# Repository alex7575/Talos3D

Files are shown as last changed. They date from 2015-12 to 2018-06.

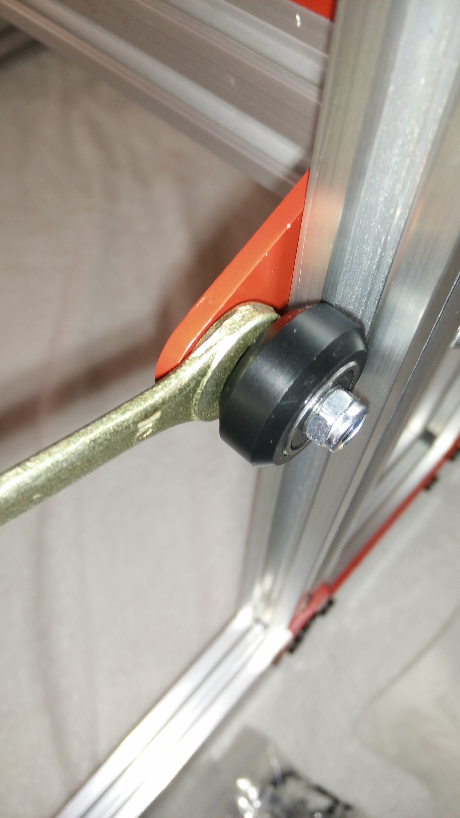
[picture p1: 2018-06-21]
Spartan/Pictures and Video/Assembly Images/IMG_20151225_152253.jpg

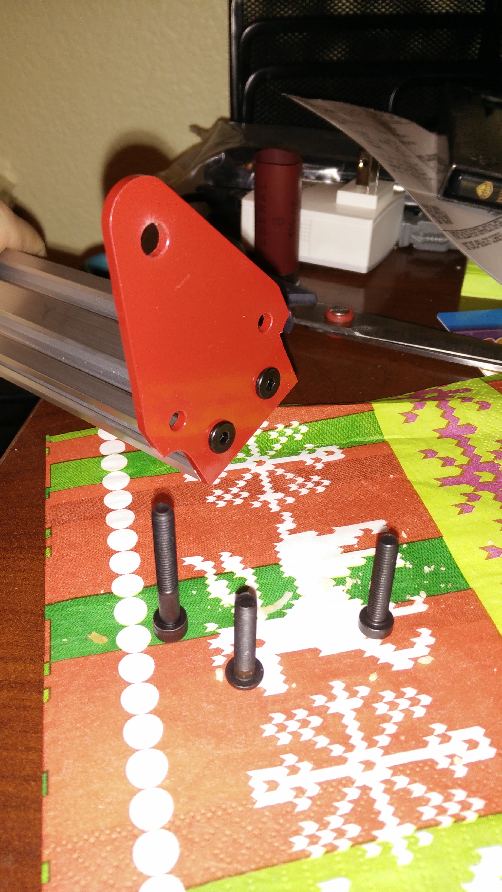
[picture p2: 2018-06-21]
Spartan/Pictures and Video/Assembly Images/IMG_20151224_170027.jpg

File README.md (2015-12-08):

# Talos3D

Please join us at our <a href="https://plus.google.com/u/0/communities/106411395795447750286">G+ group</a>



## Assembly

### Generating a Design
TODO

### Printing

### Tutorial

TODO: Tutorial on how to actually make these.

## License

All sources distributed under the [Creative Commons Attribution-NonCommercial-ShareAlike License Version 3.0](LICENSE-models).

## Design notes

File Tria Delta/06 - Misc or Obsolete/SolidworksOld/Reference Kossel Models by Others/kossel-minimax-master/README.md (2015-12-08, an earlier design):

###Kossel Minimax

Based on Johan's Kossel Mini @ github.com/jcrocholl/kossel/

Completely remodeled in Solidworks for Misumi 2020 and 2040 extrusions and a much bigger print area (300mm diameter print plate, ~470mm cylindrical print height, ~500mm tower print height, 1000mm overall height)

**Basic BOM:**

For belts, thid design uses 2020mm GT2 belts for each axis, 6060mm total, get a bit more to be safe.

* Aluminum Extrusion 2020 (length 420mm qty3 and length 1000mm qty3) (http://us.misumi-ec.com/vona2/detail/110302368740/ Choose Carefully!)
* Aluminum Extrusion 2040 (length 420mm qty3)  (http://us.misumi-ec.com/vona2/detail/110302368830/ - Choose Carefully!)
* Bag of extrusion nuts (qty1) HNKK5-3 (http://us.misumi-ec.com/vona2/detail/110302246940/)
* 300mm diameter round glass plate (such as http://www.amazon.com/Clear-Borosilicate-Glass-Printers-Round/dp/B00GRHFIC0)

Kossel Mini fasteners BOM, bearings BOM, 3x Nema  17 motors for motion, bowden extruder of your choice with enough bowden tube

**The design has 3 different types of vertical movement types available:**

1. *Steel Linear bearing:* MGN 12H rails and bearing cartridges, 600mm (like http://www.ebay.com/itm/161304571537)
  - Pros: superior rigidity, longevity, and backlash tolerances. Not a lot of material to print. 
  - Cons: expensive (over 150$USD for three 800mm long rails with bearings)
 
2. *Printed linear bearing:* Uses 5/16th delrin balls found on amazon (http://www.amazon.com/gp/product/B000FMWFXI/ 2 packs). 
  - Pros: Bearings are cheap, about $10 for plenty of balls, decent longevity, nearly fully 3d printed solution
  - Cons: Can be noisy, and requires a good printer to make bearings with smooth channels to facilitate smooth travel. 
	
3. *Printed linear bushings:* PLA bushings that slide over the extrusions.
  - Pros: Fully 3d-printed solution, lightweight solution, can be assembled and tightened with zip-ties
  - Cons: May wear over time requiring replacement or tightening to eliminate backlash and wobble.

Kossel mini assembly instructions apply, with a slight difference on the upper vertex:

  There is an embedded nut trap on the inside of the bearing area. On top of that is a single washer followed by the two flanged bearings, and then another washer.
  
  The tensioner could use a larger washer than the Kossel mini's instruction, or perhaps some printed solution. I use an additional set of m4 washers under the m3 washers.

*TODO:*

Design effector plate, extruder fan shroud, auto level probe mount.
  
  You can use regular Kossel mini parts for these if you want to print it now.

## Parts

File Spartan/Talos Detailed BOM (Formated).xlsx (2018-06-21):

MAIN SUB-ASMB | SUB-ASMB (.X) | SUB-ASMB (.X.X) | SUB-ASMB NAME | PART NUMBER | DESCRIPTION | ASMB QTY: | QTY PER SUB-ASMB | QTY | URL LINK
1 |  |  | Frame |  |  | 1
 | 1.1 |  |  | V-slot 20x80x400 | V-slot 20x80x400 |  | 2 | 2
 | 1.2 |  |  | V-slot 20x60x370 | V-slot 20x60x370 |  | 2 | 2
 | 1.3 |  |  | V-slot 20x20x340 | V-slot 20x20x340 |  | 4 | 4
 | 1.4 |  |  | V-slot 20x20x370 | V-slot 20x20x370 |  | 2 | 2
 | 1.6 |  |  | V-slot 20x20x400 | V-slot 20x20x400 |  | 2 | 2
2 |  |  | Corner Bracket ASMB |  |  | 4
 | 2.1 |  |  | Corner Bracket | CNC Cut Aluminum Plate |  | 1 | 4
 | 2.2 |  |  | M5 x 8 | Low Profile Screw M5 x 8 |  | 5 | 20
 | 2.3 |  |  | Tee Nut | Tee Nut |  | 5 | 20
3 |  |  | Side Panel ASMB |  |  | 2
 | 3.1 |  |  | Side Panel Plate | CNC Cut Aluminum Plate |  | 1 | 2
 | 3.2 |  |  | M5 x 8 | Low Profile Screw M5 x 8 |  | 8 | 16
 | 3.3 |  |  | Tee Nut | Tee Nut |  | 8 | 16
4 |  |  | Top Motor Plate ASMB |  |  | 2
 | 4.1 |  |  | Top Motor Plate | CNC Cut Aluminum Plate |  | 1 | 2
 | 4.2 |  |  | Z-NEMA17 | Nema17 with Integrated Leadscrew |  | 1 | 2
 | 4.3 |  |  | M5 x 8 | Low Profile Screw M5 x 8 |  | 4 | 8
 | 4.4 |  |  | M5 x 20 | Low Profile Screw M5 x 20 |  | 2 | 4
 | 4.5 |  |  | Tee Nut | Tee Nut |  | 4 | 8
5 |  |  | Lower Bracket ASMB |  |  | 4
 | 5.1 |  |  | Lower Bracket Plate | CNC Cut Aluminum Plate |  | 1 | 4
 | 5.2 |  |  | M5 x 20 | Low Profile Screw M5 x 20 |  | 4 | 16
 | 5.3 |  |  | M5 x 8 | Low Profile Screw M5 x 8 |  | 3 | 12
 | 5.4 |  |  | Tee Nut | Tee Nut |  | 3 | 12
6 |  |  | Gantry ASMB |  |  | 1
 | 6.1 |  |  | V-Slot 20x40x360 X-Gantry | V-slot 20x40x360 |  | 1 | 1
 | 6.2 |  | Gantry Plate ASMB |  |  |  | 2
 |  | 6.2.1 |  | Gantry Plate | CNC Cut Aluminum Plate |  |  | 2
 |  | 6.2.2 |  | Solid V Wheel | Openbuilds Delrin Wheel Assembly |  |  | 6
 |  | 6.2.3 |  | Eccentric Spacer 1/4" | 1/4" Eccentric Spacer |  |  | 2
 |  | 6.2.4 |  | Aluminum Spacer 1/4" | 1/4" Aluminum Spacer |  |  | 4
 |  | 6.2.5 |  | M5 x 25 | Low Profile Screw M5 x 25 |  |  | 6
 |  | 6.2.6 |  | M5 x 20 | Low Profile Screw M5 x 20 |  |  | 4
 | 6.3 |  | Lead Screw Plate With Motor ASMB |  |  |  | 1
 |  | 6.3.1 |  | Lead Screw Plate with Motor | CNC Cut Aluminum Plate |  |  | 1
 |  | 6.3.2 |  | M5 x 8 | Low Profile Screw M5 x 8 |  |  | 1
 |  | 6.3.3 |  | M3 x 12 | Button Head Socket Cap Screw M3 x 12 |  |  | 4
 |  | 6.3.4 |  | 40MM_NEMA17 | Nema17 (40mm Long) |  |  | 1
 |  | 6.3.5 |  | Smooth Idler | Openbuilds Delrin Smooth Idler Assembly |  |  | 1
 |  | 6.3.6 |  | Precision Shim 10 x 5 x 1 | Precision Shim 10 x 5 x 1 |  |  | 2
 |  | 6.3.7 |  | M5 x 25 | Low Profile Screw M5 x 25 |  |  | 1
 |  | 6.3.8 |  | Aluminum Spacer 1/4" | 1/4" Aluminum Spacer |  |  | 1
 |  | 6.3.9 |  | Tee Nut | Tee Nut |  |  | 2
 |  | 6.3.10 |  | GT2 Timing Pulley 20 Tooth | GT2 Timing Pulley 20 Tooth |  |  | 1
 |  | 6.3.11 |  | Leadscrew Nut | Leadscrew Nut |  |  | 1
 |  | 6.3.12 |  | M3 x 8 | Button Head Socket Cap Screw M3 x 8 |  |  | 3
 | 6.4 |  | Lead Screw Plate With Idler ASMB |  |  |  | 1
 |  | 6.4.1 |  | Lead Screw Plate (Idler) | CNC Cut Aluminum Plate |  |  | 1
 |  | 6.4.2 |  | M5 x 30 | Low Profile Screw M5 x 30 |  |  | 1
 |  | 6.4.3 |  | M5 x 8 | Low Profile Screw M5 x 8 |  |  | 1
 |  | 6.4.4 |  | Tee Nut | Tee Nut |  |  | 2
 |  | 6.4.5 |  | Smooth Idler | Openbuilds Delrin Smooth Idler Assembly |  |  | 1
 |  | 6.4.6 |  | Precision Shim 10 x 5 x 1 | Precision Shim 10 x 5 x 1 |  |  | 2
 |  | 6.4.7 |  | Aluminum Spacer 1/4" | 1/4" Aluminum Spacer |  |  | 1
 |  | 6.4.8 |  | Leadscrew Nut | Leadscrew Nut |  |  | 1
 |  | 6.4.9 |  | M3 x 8 | Button Head Socket Cap Screw M3 x 8 |  |  | 3
7 |  |  | X_Carriage_Universal |  |  | 1
 | 7.1 |  |  | X Carriage Universal Plate | CNC Cut Aluminum Plate |  | 1 | 1
 | 7.2 |  |  | Delrin Mini V Wheel | Openbuilds Delrin Mini Wheel Assembly |  | 2 | 2
 | 7.3 |  |  | Aluminum Spacer 1/4" | 1/4" Aluminum Spacer |  | 2 | 2
 | 7.4 |  |  | M5 x 25 | Low Profile Screw M5 x 25 |  | 3 | 3
 | 7.5 |  |  | Solid V Wheel | Openbuilds Delrin Wheel Assembly |  | 1 | 1
 | 7.6 |  |  | Eccentric Spacer 1/4" | Eccentric Spacer 6mm |  | 1 | 1
 | 7.7 |  |  | Shim 10 x 5 x 0.2 | Shim 10 x 5 x 0.2 |  | 1 | 1
 | 7.8 |  |  | M3 Hex Nut | M3 Hex Nut |  | 6 | 6
 | 7.9 |  |  | M3 Nylon Insert Lock Nut | M3 Nylon Insert Lock Nut |  | 2 | 2
 | 7.10 |  |  | Inductive Level Probe | Inductive Level Probe |  | 1 | 1
 | 7.11 |  |  | 4020Blower | 40x40x20 Blower Fan |  | 1 | 1
 | 7.12 |  |  | E3D All Metal Hotend | E3D All Metal Hotend |  | 1 | 1
 | 7.13 |  |  | Bondtech Mini | Bondtech Mini Extruder Drive |  | 1 | 1
 | 7.14 |  |  | 30x30_Fan (from E3D Hotend Kit) | 30x30 Fan |  | 1 | 1
 | 7.15 |  |  | M3 x 8 | Button Head Socket Cap Screw M3 x 8 |  | 4 | 4
 | 7.16 |  |  | M3 x 10 | Button Head Socket Cap Screw M3 x 10 |  | 2 | 2
 | 7.17 |  |  | M3 x 12 | Button Head Socket Cap Screw M3 x 12 |  | 10 | 10
 | 7.18 |  |  | Part Cooling Fan Discharge Duct | Printed Part |  | 1 | 1
 | 7.19 |  |  | Hotend Retainer Clip | Printed Part |  | 1 | 1
 | 7.20 |  |  | Belt Connector Body | Printed Part |  | 1 | 1
 | 7.21 |  |  | Belt Connector | Printed Part |  | 1 | 1
 | 7.22 |  |  | Probe Mount | Printed Part |  | 1 | 1
8 |  |  | Heated Bed and Carriage |  |  | 1
 | 8.1 |  |  | HB Mounting Plate | CNC Cut Aluminum Plate |  | 1 | 1
 | 8.2 |  |  | Solid V Wheel | Openbuilds Delrin Wheel Assembly |  | 4 | 4
 | 8.3 |  |  | Eccentric Spacer 1/4" | 1/4" Eccentric Spacer |  | 2 | 2
 | 8.4 |  |  | Aluminum Spacer 1/4" | 1/4" Aluminum Spacer |  | 2 | 2
 | 8.5 |  |  | M5 x 30 | Low Profile Screw M5 x 30 |  | 4 | 4
 | 8.6 |  |  | MK3 Aluminum Heated Bed | MK3 Aluminum Heated Bed |  | 1 | 1
 | 8.7 |  |  | M3 Nylon Insert Lock Nut | M3 Nylon Insert Lock Nut |  | 7 | 7
 | 8.8 |  |  | M3 x 8 | Button Head Socket Cap Screw M3 x 8 |  | 4 | 4
 | 8.9 |  |  | Bed Spring (Mcmaster 9657K275) | Spring OD .36", Wire 0.041", Length 0.5" |  | 4 | 4
 | 8.10 |  |  | M3 Oversized Washer (91116A120) | M3 Oversized Washer (91116A120) |  | 4 | 4
 | 8.11 |  |  | M3 Flat Washer (91116A120) | M3 Flat Washer (91116A120) |  | 4 | 4
 | 8.12 |  |  | Nut Knob | CNC Cut Aluminum Plate |  | 4 | 4
 | 8.13 |  |  | M3 Hex Nut | M3 Hex Nut |  | 4 | 4
 | 8.14 |  |  | Y Belt Clip | Printed Part |  | 1 | 1
 | 8.15 |  |  | M3 x 12 | Button Head Socket Cap Screw M3 x 12 |  | 3 | 3
9 |  |  | New Y Axis Motor Drive |  |  | 1
 | 9.1 |  |  | Y Motor Mount Plate | CNC Cut Aluminum Plate |  | 1 | 1
 | 9.2 |  |  | 40MM_NEMA17 | Nema17 (40mm Long) |  | 1 | 1
 | 9.3 |  |  | M3 x 10 | Button Head Socket Cap Screw M3 x 10 |  | 4 | 4
 | 9.4 |  |  | M5 x 25 | Low Profile Screw M5 x 25 |  | 1 | 1
 | 9.5 |  |  | M5 x 8 | Low Profile Screw M5 x 8 |  | 1 | 1
 | 9.6 |  |  | Tee Nut | Tee Nut |  | 2 | 2
 | 9.7 |  |  | GT2 Timing Pulley 20 Tooth | GT2 Timing Pulley 20 Tooth |  | 1 | 1
 | 9.8 |  |  | Smooth Idler | Openbuilds Delrin Smooth Idler Assembly |  | 1 | 1
 | 9.9 |  |  | Precision Shim 10 x 5 x 1 | Precision Shim 10 x 5 x 1 |  | 2 | 2
10 |  |  | Y Front Idler |  |  | 1
 | 10.1 |  |  | Smooth Idler | Openbuilds Delrin Smooth Idler Assembly |  | 1 | 1
 | 10.2 |  |  | Aluminum Spacer 1/8" | 1/8" Aluminum Spacer |  | 1 | 1
 | 10.3 |  |  | M5 Oversized Washer (91100A140) | M5 Oversized Washer (91100A140) |  | 1 | 1
 | 10.4 |  |  | Tee Nut | Tee Nut |  | 1 | 1
 | 10.5 |  |  | M5 x 25 | Low Profile Screw M5 x 25 |  | 1 | 1
 | 10.6 |  |  | Precision Shim 10 x 5 x 1 | Precision Shim 10 x 5 x 1 |  | 1 | 1
11 |  |  | Y Plate ASMB |  |  | 2
 | 11.1 |  |  | Y Front Plate | CNC Cut Aluminum Plate |  | 1 | 2
 | 11.2 |  |  | M5 x 20 | Low Profile Screw M5 x 20 |  | 2 | 4
 | 11.3 |  |  | M5 x 8 | Low Profile Screw M5 x 8 |  | 6 | 12
 | 11.4 |  |  | Tee Nut | Tee Nut |  | 6 | 12
 | 11.5 |  |  | Cast Corner Bracket | Cast Corner Bracket |  | 2 | 4
12 |  |  | Power_Supply ASMB |  |  | 1
 | 12.1 |  |  | 360W_12V_Powersupply | Switching Power Supply |  | 1 | 1
 | 12.2 |  |  | PSU Holder | Printed or Machined part |  | 2 | 2
 | 12.3 |  |  | M4 x 6mm | Buttonhead M4 x 6mm Long |  | 6 | 6
 | 12.4 |  |  | M5 x 8 | Low Profile Screw M5 x 8 |  | 4 | 4
 | 12.5 |  |  | Tee Nut | Tee Nut |  | 5 | 5
 | 12.6 |  |  | Wiring Safety Cover | Printed Part |  | 1 | 1
 | 12.7 |  |  | Electrical Fused Plug | Plug/Switch/Fuse Module |  | 1 | 1
 | 12.8 |  |  | M5 x 10 | Low Profile Screw M5 x 10 |  | 1 | 1
13 |  |  | Controler_Assembly |  |  | 1
 | 13.1 |  |  | GT2560 Case - Bottom | Printed part |  | 1 | 1
 | 13.2 |  |  | GT2560 Case - Top | Printed Part |  | 1 | 1
 | 13.3 |  |  | Geeetech_GT2560 | Geeetech GT2560 Printer Control Board |  | 1 | 1
 | 13.4 |  |  | ATX-12V-4-Pin Plug or Jumper | Power Plug to Power Board |  | 1 | 1
 | 13.5 |  |  | M5 x 8 | Low Profile Screw M5 x 8 |  | 3 | 3
 | 13.6 |  |  | Tee Nut | Tee Nut |  | 3 | 3
 | 13.7 |  |  | M3 x 8 | Button Head Socket Cap Screw M3 x 8 |  | 8 | 8
 | 13.8 |  |  | 40x40x10 Cooling Fan | 40x40x10 Cooling Fan |  | 1 | 1
 | 13.9 |  |  | M3 x 12 | Button Head Socket Cap Screw M3 x 12 |  | 4 | 4
 | 13.10 |  |  | M3 Hex Nut | M3 Hex Nut |  | 4 | 4
14 |  |  | Geetech_GT2560_LCD_Box_ASMB |  |  | 1
 | 14.1 |  |  | Geetech_GT2560_LCD | LCD Controller |  | 1 | 1
 | 14.2 |  |  | Geetech_GT2560_LCD_Front_Cover | Printed Part |  | 1 | 1
 | 14.3 |  |  | Geetech_GT2560_LCD_Back_Cover | Printed Part |  | 1 | 1
 | 14.4 |  |  | M5 x 8 | Low Profile Screw M5 x 8 |  | 4 | 4
 | 14.5 |  |  | Tee Nut | Tee Nut |  | 4 | 4
 | 14.6 |  |  | M3 x 8 | Button Head Socket Cap Screw M3 x 8 |  | 6 | 6
15 |  |  | Spool Holder (Fixed Side) |  |  | 2
 | 15.1 |  |  | Cast Corner Bracket | Cast Corner Bracket |  | 1 | 2
 | 15.2 |  |  | Smooth Idler | Openbuilds Delrin Smooth Idler Assembly |  | 1 | 2
 | 15.3 |  |  | M5 x 8 | Low Profile Screw M5 x 8 |  | 1 | 2
 | 15.4 |  |  | Aluminum Spacer 1/4" | 1/4" Aluminum Spacer |  | 1 | 2
 | 15.5 |  |  | M5 x 30 | Low Profile Screw M5 x 30 |  | 1 | 2
 | 15.6 |  |  | Tee Nut | Tee Nut |  | 1 | 2
 | 15.7 |  |  | Nylon Insert Lock Nut M5 | Nylon Insert Lock Nut M5 |  | 1 | 2
 | 15.8 |  |  | Precision Shim 10 x 5 x 1 | Precision Shim 10 x 5 x 1 |  | 1 | 2
16 |  |  | Spool Holder (Floating Side) |  |  | 2
 | 16.1 |  |  | Cast Corner Bracket | Cast Corner Bracket |  | 1 | 2
 | 16.2 |  |  | Smooth Idler | Openbuilds Delrin Smooth Idler Assembly |  | 1 | 2
 | 16.3 |  |  | M5 x 8 | Low Profile Screw M5 x 8 |  | 1 | 2
 | 16.4 |  |  | M5 x 45 | Low Profile Screw M5 x 45 |  | 1 | 2
 | 16.5 |  |  | Tee Nut | Tee Nut |  | 1 | 2
 | 16.6 |  |  | Nylon Insert Lock Nut M5 | Nylon Insert Lock Nut M5 |  | 2 | 4
 | 16.7 |  |  | Precision Shim 10 x 5 x 1 | Precision Shim 10 x 5 x 1 |  | 1 | 2

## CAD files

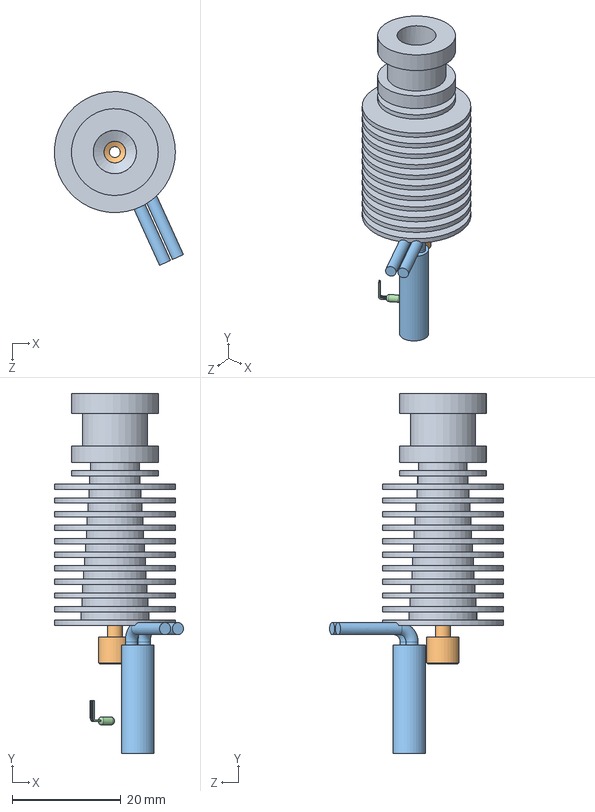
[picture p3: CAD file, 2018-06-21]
Tria Delta/01 - User Mods/Eric Lien/Delta Effector 3 ASMB/03 - Solidworks/E3D All Metal Hotend V6 assy.SLDASM
23.8 x 66.3 x 32.0 mm
E3D v6 HotEnd - HeatsinkV2
E3D v6 HotEnd - Heatbreak
Ceramic Cartridge HeaterV2
Thermistor

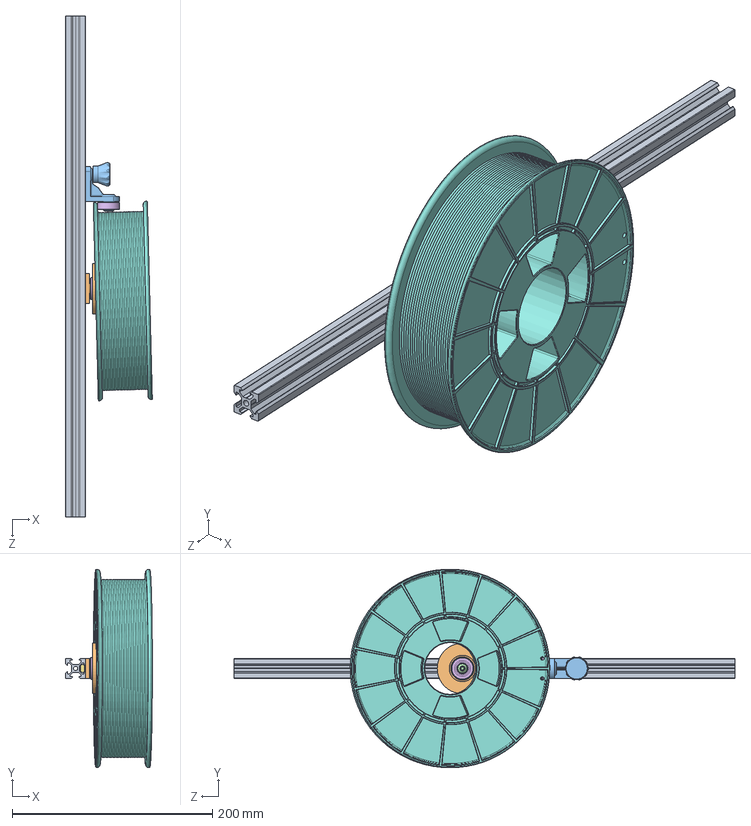
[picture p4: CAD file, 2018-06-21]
Tria Delta/02 - 3D CAD Models/Solidworks (Latest Version)/Printed Parts/Mini_Spool_Holder/Mini Spool Holder.SLDASM
86.6 x 197.9 x 500.0 mm
Mini Spool Holder Hub
Mini Spool Holder Top Idler V3
91239A236_CLASS 10.9 STL BUTTON-HEAD SOCKET CAP SCREW
91290A228_BLACK-OXIDE CLASS 12.9 SOCKET HEAD CAP SCREW
5972K501_BALL BEARING x 3
Spring Loaded Tee Nut x 2
Spool

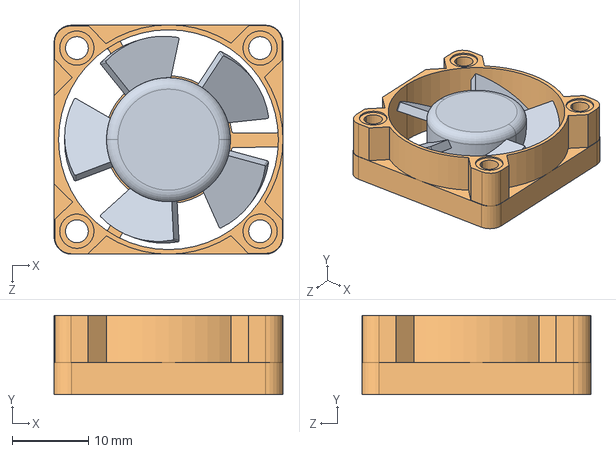
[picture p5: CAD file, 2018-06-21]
Tria Delta/02 - 3D CAD Models/Solidworks (Latest Version)/Reference Parts/Electronics/30x30_Fan.SLDASM
30.0 x 10.4 x 30.0 mm
D3010_SOLID_1
D3010_QUILT_1

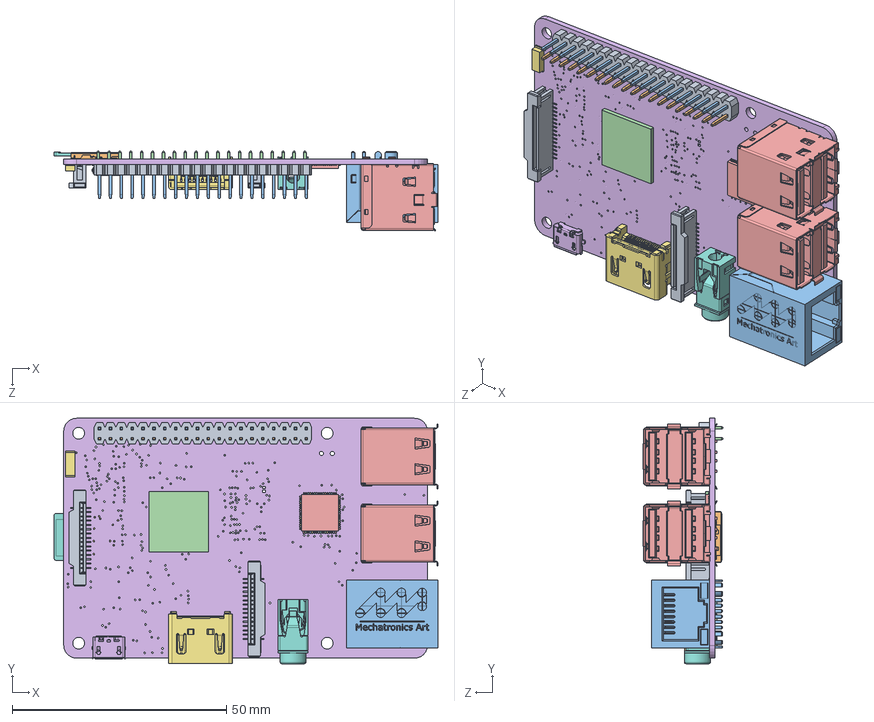
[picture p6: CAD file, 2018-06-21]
Tria Delta/02 - 3D CAD Models/Solidworks (Latest Version)/Reference Parts/Electronics/PI3/Raspberry Pi 3.SLDASM
89.6 x 57.3 x 18.6 mm
Raspberry Pi 3157
Raspberry Pi 3242 x 20
Raspberry Pi 3266 x 20
raspberry_pi_3(bar_180_2x20)
MOLEX_672983090 x 2
molex_0473460001
molex_0471510001
PJ-322
te_1-1734248-5 x 2
MOLEX_1040310811
raspberry_pi_B_(RJ45)
Raspberry Pi 312
Raspberry Pi 314
Raspberry Pi 3172
Raspberry Pi 3173
Raspberry Pi 3174
Raspberry Pi 3175
Raspberry Pi 3176
Raspberry Pi 3177
Raspberry Pi 3178
Raspberry Pi 3179
Raspberry Pi 3180
Raspberry Pi 3181
Raspberry Pi 3182
Raspberry Pi 3183
Raspberry Pi 3184
Raspberry Pi 3185
Raspberry Pi 3186
Raspberry Pi 3187
Raspberry Pi 3188
Raspberry Pi 3189
Raspberry Pi 3190
Raspberry Pi 3191
Raspberry Pi 3192
Raspberry Pi 3193
Raspberry Pi 3194
Raspberry Pi 3195
Raspberry Pi 3196
Raspberry Pi 3197
Raspberry Pi 3198
Raspberry Pi 3199
Raspberry Pi 3200
Raspberry Pi 3201
Raspberry Pi 3202
Raspberry Pi 3203
Raspberry Pi 3204
Raspberry Pi 3205
Raspberry Pi 3206
Raspberry Pi 3207
Raspberry Pi 3208
Raspberry Pi 3209
Raspberry Pi 3210
Raspberry Pi 3211
Raspberry Pi 3212
Raspberry Pi 3213
Raspberry Pi 3214
Raspberry Pi 3215
Raspberry Pi 3216
Raspberry Pi 3217
Raspberry Pi 3218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

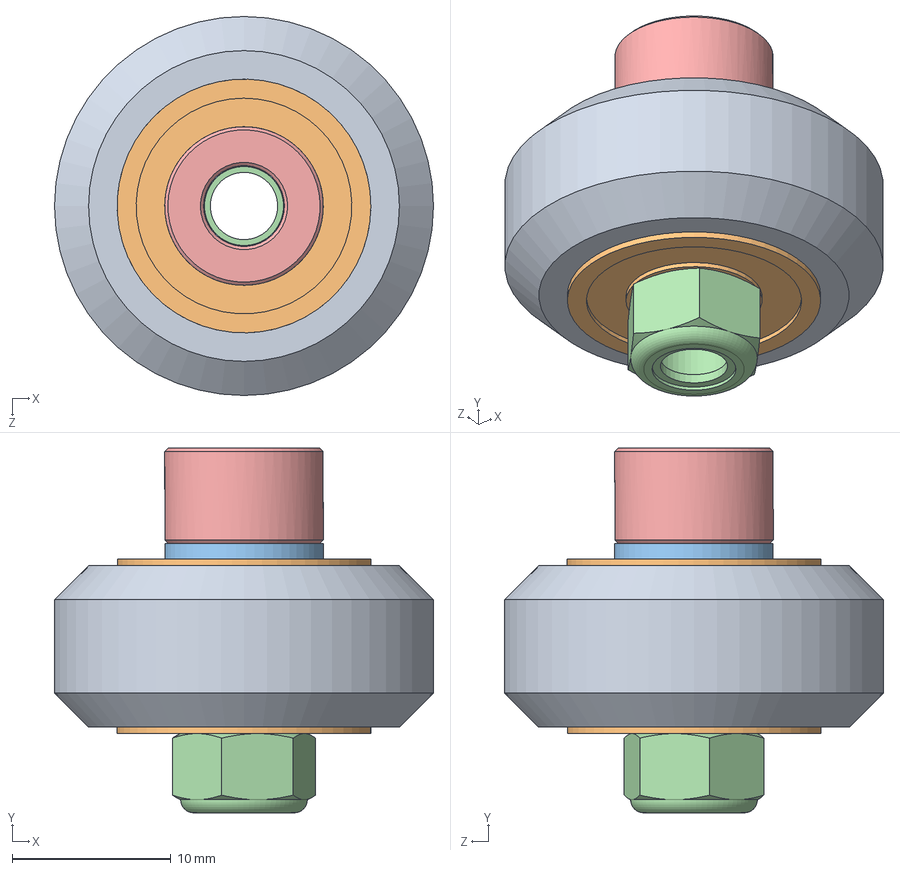
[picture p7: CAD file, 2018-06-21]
Tria Delta/02 - 3D CAD Models/Solidworks (Latest Version)/Reference Parts/OpenBuilds Solidworks Library/Assemblies/Wheels/Solid V Wheel.SLDASM
23.9 x 23.0 x 23.9 mm
Solid V Wheel
Ball Bearing 5 x 16 x 5 x 2
Precision Shim 10 x 5 x 1 x 2
Nylon Insert Lock Nut M5
Aluminum Spacer

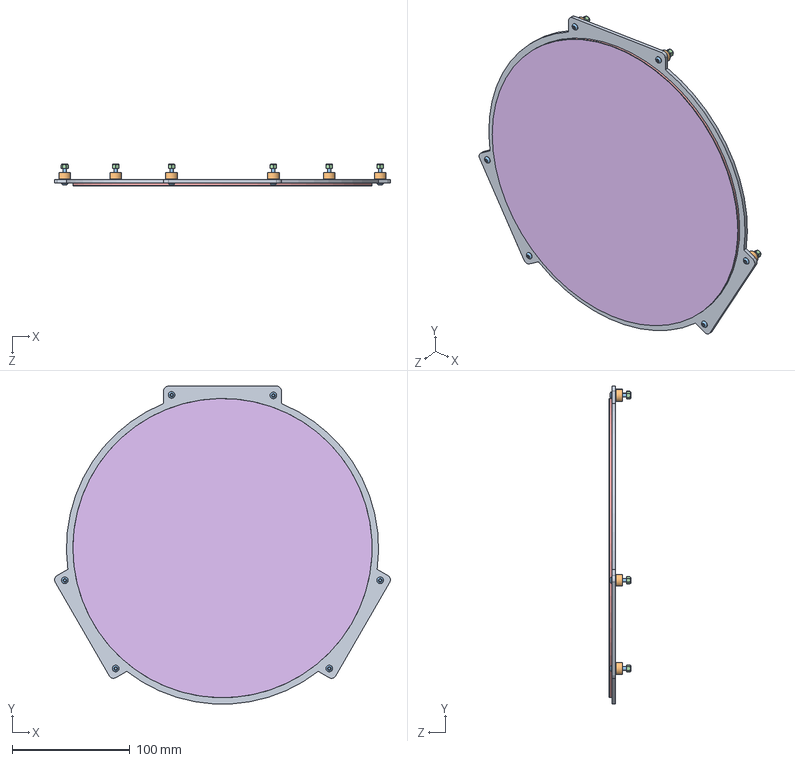
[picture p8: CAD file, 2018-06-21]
Tria Delta/02 - 3D CAD Models/Solidworks (Latest Version)/Reference Parts/SubASMB/Heated Bed.SLDASM
285.2 x 269.8 x 18.8 mm
HeatedBed
Aluminum Spacer 6mm x 6
Button Head Socket Cap Screw M3 x 6
Nylon Insert Lock Nut M3 x 6
Micheals 10in Round Mirror Glass (Item 10319993)
10in Round PEI SHeet

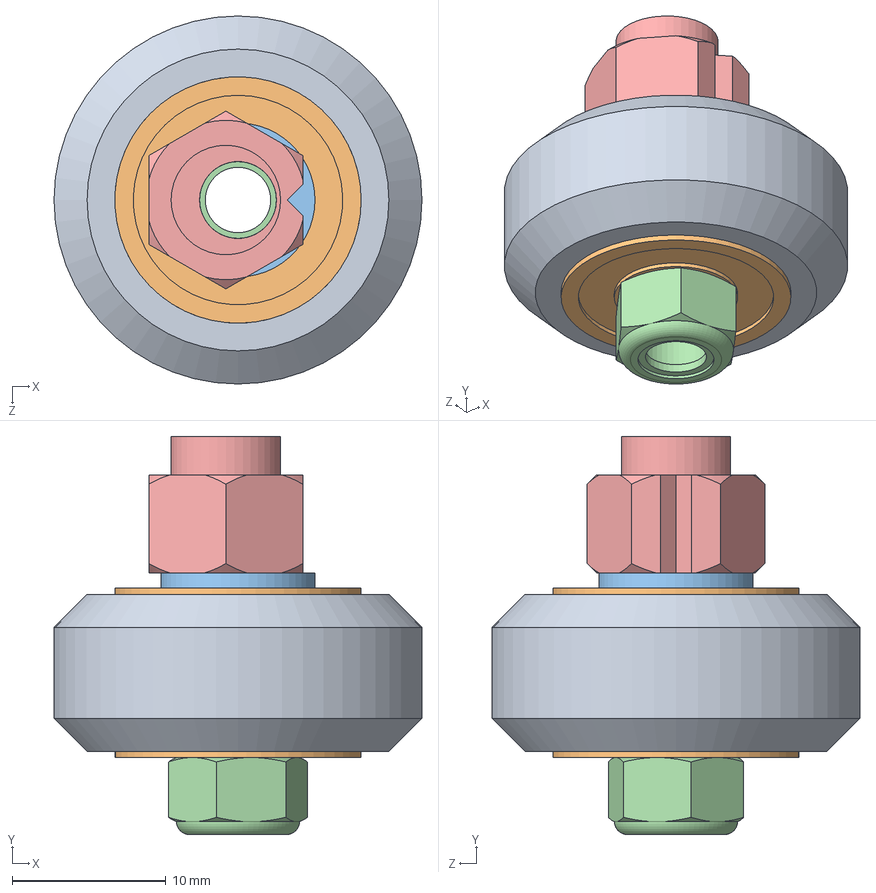
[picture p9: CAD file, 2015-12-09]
Tria Delta/Solidworks/Reference Parts/OpenBuilds Solidworks Library/Assemblies/Wheels/Solid V Wheel Eccentric.SLDASM
23.9 x 25.9 x 23.9 mm
Solid V Wheel
Ball Bearing 5 x 16 x 5 x 2
Precision Shim 10 x 5 x 1 x 2
Nylon Insert Lock Nut M5
Eccentric Spacer 6mm

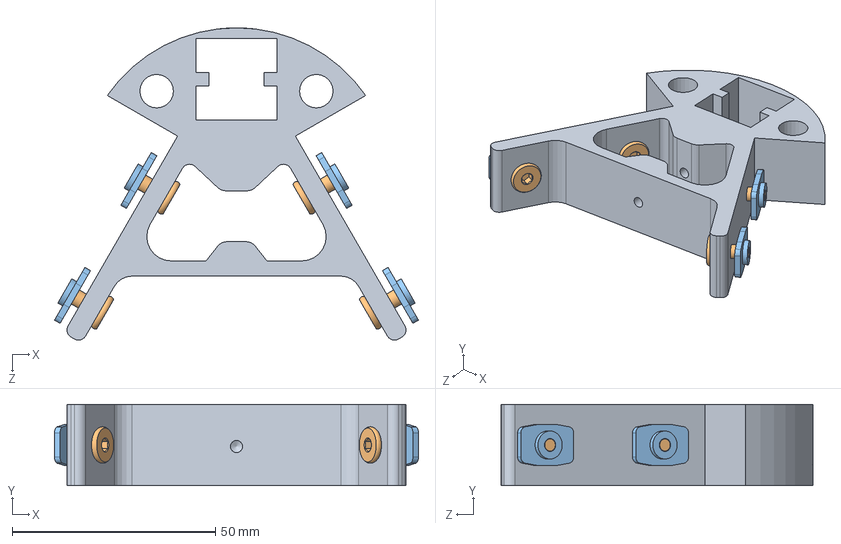
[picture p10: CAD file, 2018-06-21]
Tria Delta/02 - 3D CAD Models/Solidworks (Latest Version)/Reference Parts/SubASMB/Upper Vertex.SLDASM
89.7 x 20.0 x 76.9 mm
Vertex
Low Profile Screw M4 x 4
Tee Nut M4 x 4

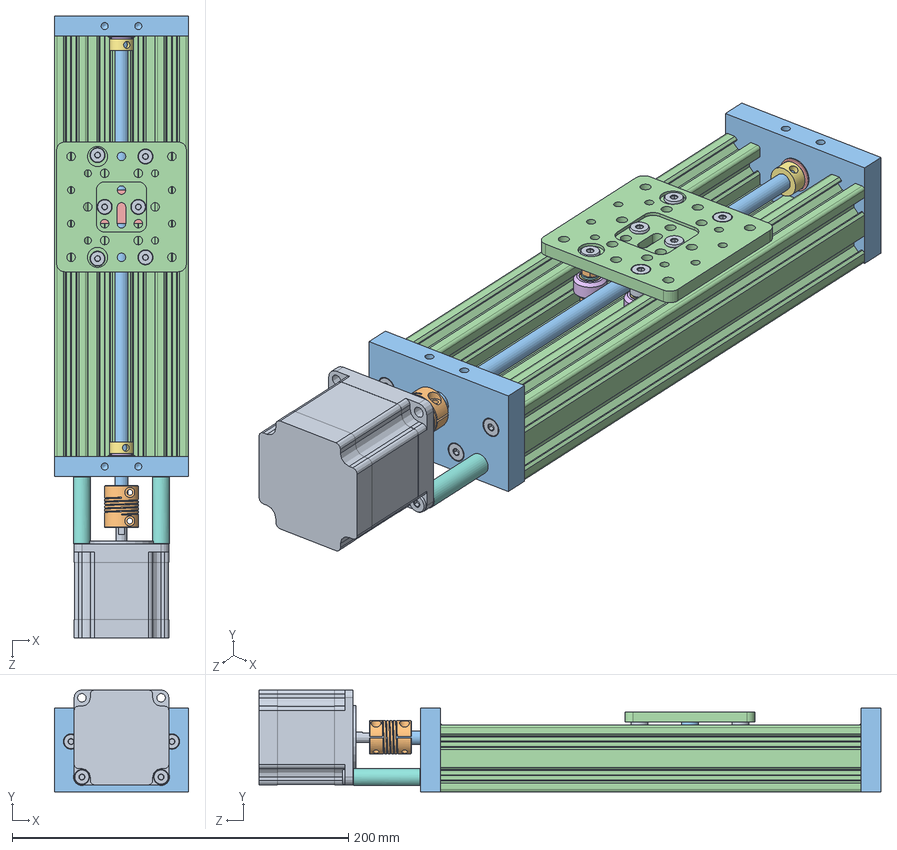
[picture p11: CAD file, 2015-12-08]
Tria Delta/Solidworks/Reference Parts/OpenBuilds Solidworks Library/Assemblies/C-Beam Linear Actuator/C-Beam Linear Actuator 250mm.SLDASM
80.0 x 60.7 x 370.0 mm
Low Profile Screw M5 x 16
Nylon Insert Lock Nut M5 x 6
C-Beam End Mount x 2
C-Beam 40x80x250 Linear Rail
Ball Bearing 8 x 16 x 5 x 2
Shim Washer 8mm x 2
Lock Collar 8mm x 2
Aluminum Spacer 40mm x 2
Nema 23 Stepper Motor
Flexible Coupling 0.25in x 8mm
8mm leadscrew 290mm
C-Beam Gantry Plate
8mm Acme Nut Block
Xtreme Mini V Wheel x 4
Ball Bearing 5 x 10 x 4.2 x 8
Precision Shim 8 x 5 x 1 x 8
Aluminum Spacer 6mm x 2
Mini Eccentric Spacer 6mm x 2
Aluminum Spacer 3mm x 2

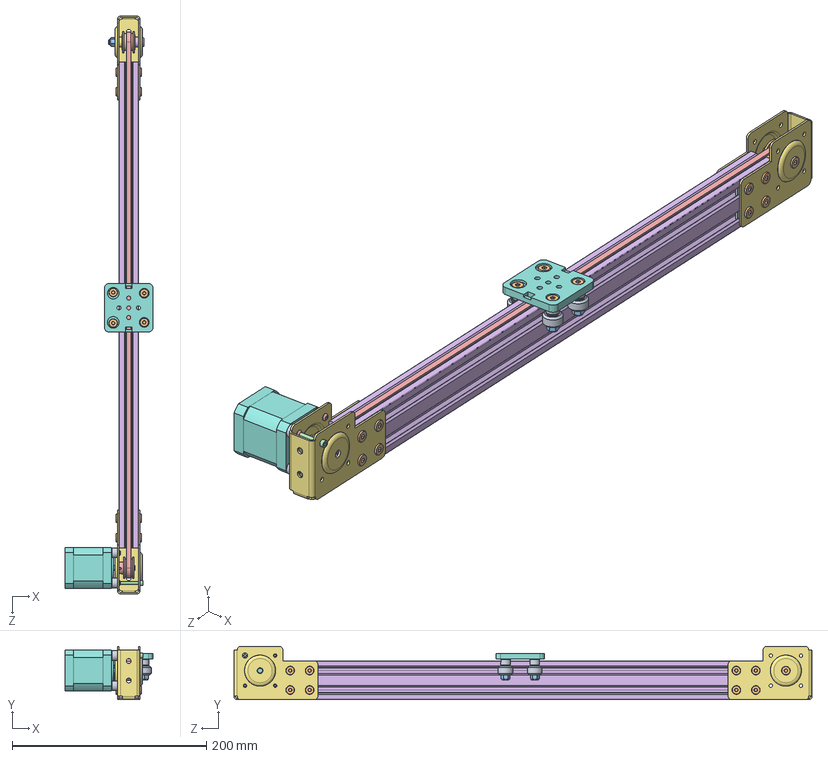
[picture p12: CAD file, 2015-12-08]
Tria Delta/Solidworks/Reference Parts/OpenBuilds Solidworks Library/Assemblies/Mini V Linear Actuator/Mini V Linear Actuator 500mm.SLDASM
90.6 x 54.9 x 594.7 mm
Double Tee Nut x 8
Low Profile Screw M5 x 21
Nylon Insert Lock Nut M5 x 5
Button Head Socket Cap Screw M3 x 4
V-Slot 20x40x500 Linear Rail
Linear Actuator End Mount x 2
Nema 17 Stepper Motor
Aluminum Spacer 6mm x 6
Smooth Idler Pulley Wheel
Ball Bearing 5 x 16 x 5 x 2
Nylon Spacer 0.125in
GT2 Timing Pulley 30 Tooth
Aluminum Spacer .25in
Aluminum Spacer .125in
Mini V Wheel Plate
Delrin Mini V Wheel x 4
Ball Bearing 5 x 10 x 4.2 x 8
Precision Shim 8 x 5 x 1 x 8
Mini Eccentric Spacer 6mm x 2
GT2 Belt 1140mm

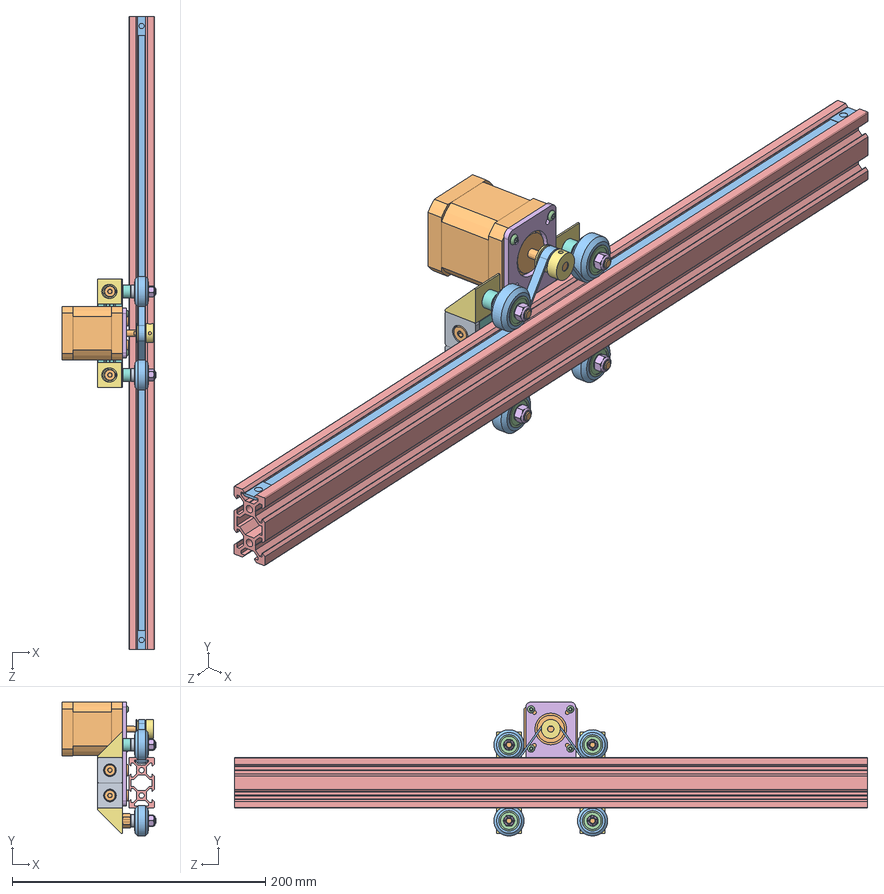
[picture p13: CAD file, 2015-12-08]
Tria Delta/Solidworks/Reference Parts/OpenBuilds Solidworks Library/Assemblies/V Slot Belt and Pinion Actuator/Mini V Slot Belt and Pinion Actuator 500mm.SLDASM
74.5 x 105.7 x 500.0 mm
Double Tee Nut x 2
Low Profile Screw M5 x 16
Tee Nut x 6
Button Head Socket Cap Screw M3 x 4
V-Slot 20x40x500 Linear Rail
Motor Mount Plate Nema 17
Black Angle Corner Connector x 4
V-Slot 20x40x80 Linear Rail
End Cap x 4
Nema 17 Stepper Motor
Solid V Wheel x 4
Ball Bearing 5 x 16 x 5 x 8
Precision Shim 10 x 5 x 1 x 4
Nylon Insert Lock Nut M5 x 4
GT2 Timing Pulley 20 Tooth
Aluminum Spacer .25in x 2
Aluminum Spacer .125in x 4
Eccentric Spacer 0.25in x 2
GT2 Belt 530mm

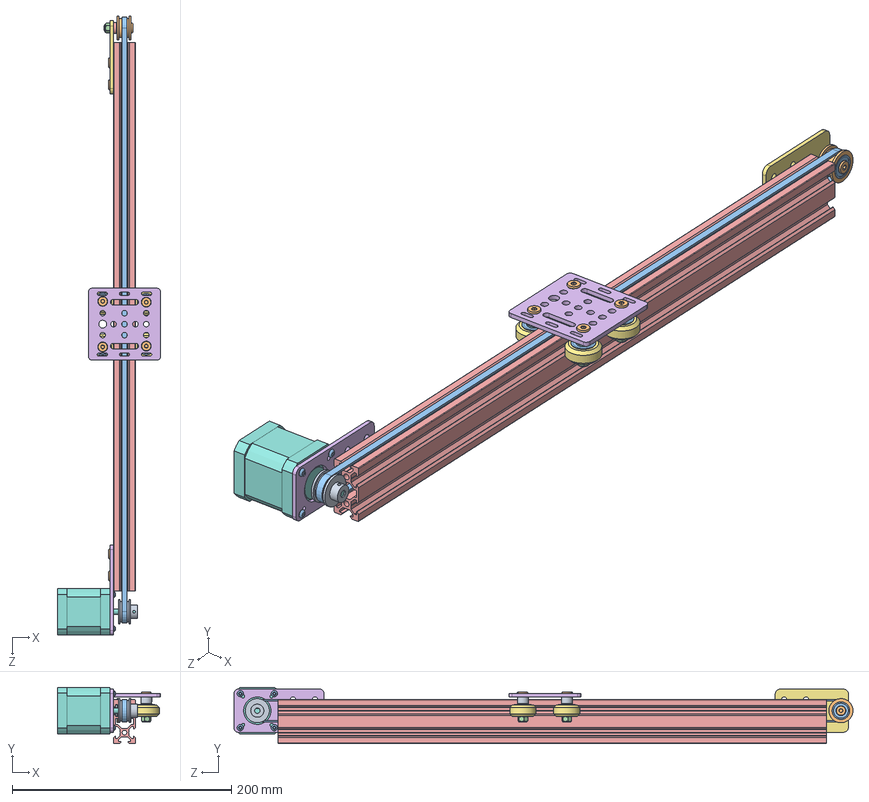
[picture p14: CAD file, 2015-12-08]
Tria Delta/Solidworks/Reference Parts/OpenBuilds Solidworks Library/Assemblies/V Slot Belt Driven Actuator/Nema 17 V Slot Belt Driven Actuator 500mm.SLDASM
93.8 x 51.2 x 564.2 mm
Double Tee Nut x 2
Low Profile Screw M5 x 9
Button Head Socket Cap Screw M3 x 4
Nylon Insert Lock Nut M5 x 5
V-Slot 20x40x500 Linear Rail
Motor Mount Plate Nema 17
Idler Pulley Plate
Nema 17 Stepper Motor
GT2 Timing Pulley 30 Tooth
Smooth Idler Pulley Wheel
Ball Bearing 5 x 16 x 5 x 10
Nylon Spacer 0.125in
Aluminum Spacer 3mm
V-Slot Gantry Plate 20mm
Solid V Wheel x 4
Precision Shim 10 x 5 x 1 x 8
Aluminum Spacer 6mm x 2
Eccentric Spacer 6mm x 2
GT2 Belt 1120mm

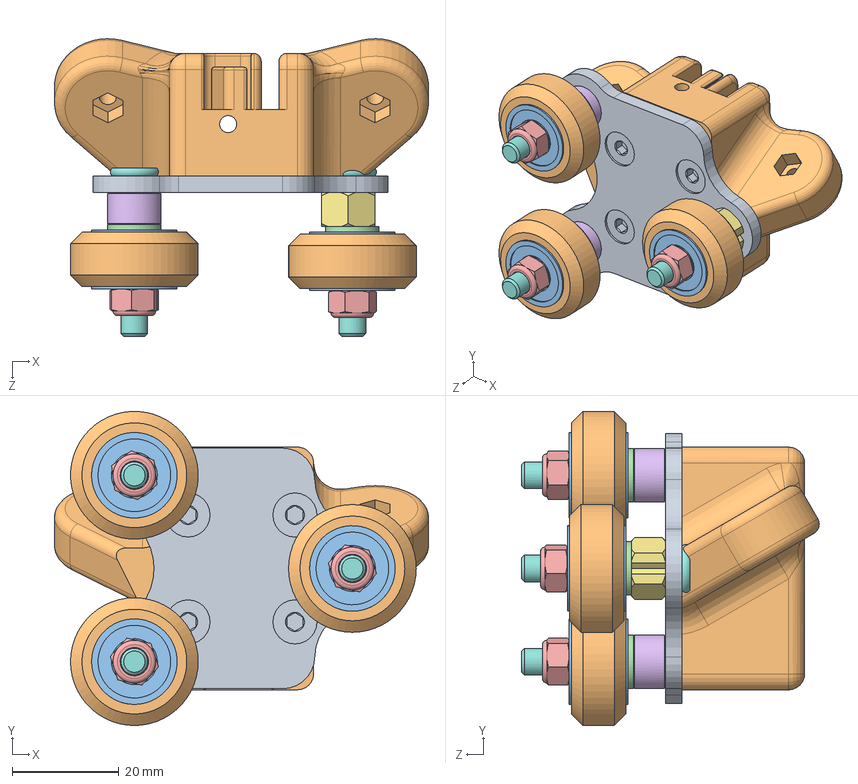
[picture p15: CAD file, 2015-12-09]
Tria Delta/Solidworks/Side Carriage.SLDASM
70.0 x 58.8 x 55.7 mm
Side Carriage
Solid V Wheel x 3
Ball Bearing 5 x 16 x 5 x 6
Precision Shim 10 x 5 x 1 x 6
Nylon Insert Lock Nut M5 x 3
Aluminum Spacer x 2
Eccentric Spacer 6mm
Low Profile Screw M5 x 3
Low Profile Screw M4 x 4
Carriage

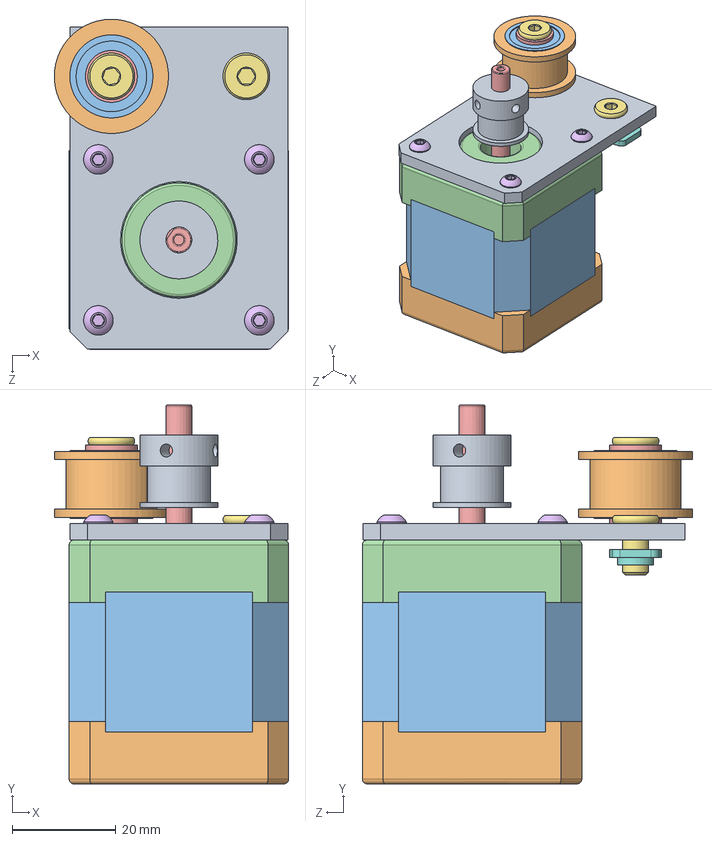
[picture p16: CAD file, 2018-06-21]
Spartan/Solidworks/Sub Assemblies/New Y Axis Motor Drive.SLDASM
45.1 x 73.0 x 63.6 mm
New Y Motor Mount
Base
FaceCap
Shaft1
Button Head Socket Cap Screw M3 x 4
Low Profile Screw M5 x 2
Tee Nut x 2
GT2 Timing Pulley 20 Tooth
Smooth Idler Pulley Wheel
Ball Bearing 5 x 16 x 5 x 2
Nylon Spacer 0.125in
Precision Shim 10 x 5 x 1 x 2

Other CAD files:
Spartan/Solidworks/Electronics/ATX-Main-24-Pin-crimp.sldprt
Tria Delta/02 - 3D CAD Models/Solidworks (Latest Version)/Reference Parts/OpenBuilds Solidworks Library/Assemblies/Wheels/Solid V Wheel Eccentric.SLDASM
Tria Delta/Solidworks/Reference Parts/OpenBuilds Solidworks Library/Assemblies/Wheels/Solid V Wheel.SLDASM
Silphium/Aluminum Spacer .25in.SLDPRT
Silphium/Case Backplate.SLDPRT
Silphium/Case Backplate.STL
Silphium/Corner Bracket.SLDPRT
Silphium/Eccentric Spacer 0.25in.SLDPRT
Silphium/GT2 Timing Pulley 20 Tooth.SLDPRT
Silphium/Gantry Plate - Front.DXF
Silphium/Gantry Plate - Front.SLDPRT
Silphium/Gantry Plate.DXF
Silphium/Gantry Plate.SLDPRT
Silphium/Gantry.SLDASM
Silphium/LCheapo Case.STL
Silphium/LCheapo.SLDASM
Silphium/Laser Heatsink.SLDPRT
Silphium/Laser.SLDPRT
Silphium/MAIN.SLDASM
Silphium/Nema 17 Stepper Motor.SLDPRT
Silphium/Part1.sldprt
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

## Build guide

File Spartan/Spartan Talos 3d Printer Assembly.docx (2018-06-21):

# Talos 3d Printer Assembly

## Step 1 – Bottom Frame

Tools needed

- 3mm allan key/wrench
- Optionally blue lock-tite
- square

Parts needed

- 2 4 high Al extrusion
- 2 3 high Al extrusion
- 16 M5 x 8mm screws
- 12 M5 extrusion nuts
- 2 7 left plate hole plates
- 2 7 hole right plates

Attach plates to the ends of the 4 high extrusions. Ensure the three holes are pointed inwards – toward each others when 4 high extrusions are aligned parallel from each other.

To avoid cross threading the steel screws in the Al extrustion, back out the screws while in the hole until you feel the screw seat properly in the hole. Then proceed to tighten the screws into the extrusions.

<see photo>

When attaching the 3 high extrusion make sure you don’t tighten the screws all the way until ALL 12 screws have been lightly threaded in the nuts. Take the square and place on the inside of corners of the extrusions and while the end of the three level extrustion is against the taller one tighten all three set screws.

## Step 2 – Print Head Assembly

Tools needed

Parts needed

- Proximity sensor
- Shrouded fen
- 30mm fan
- Belt connector body
- Part cooling fan discharge duct
- Extruder assembly
- Extruder mounts
- Stepper motor
- Extruder teeth
- Probe mount
- Hot end retainer clip
- Hot end plate
- M3 x14mm screw x5
- M3x10mm screw x6
- M3x12mm screw x2
- M3x16mm screw x2 (more like 18, but I only have 16)
- M3x20mm screw x1
- M3 nut x8
- E3d extruder – preferably fully assembled – kit
- M3x10mm round screw

Using the probe mount, Push M3x14 screw through horizontal hole and connect to M3 nut. Do not tighten this down, just get a couple of threads into the nut. Tap two vertical screw holes with M3 tap. Then using the M3x10mm screws attach to the extruder mounting plate.

Use a soldering iron to melt in plate two M3 nuts in place on the top of the hot end retainer clip. Melt a third nut into the part fan mount. Gently place the forth nut into place. Then using the m3x16mm screw attach the part fan to the hot end retainer clip. Ensure that blow how is facing down and center fan duct is facing outwards. Now take M3x20 mm and install the part fan discharge duct, lightly tighten down the duct on the fan.

Insert the fan set screws into the hot end retainer clip and screw down the 30mm fan. Ensure that the fan tables are pointed up in relationship to the mount. At this point place the hot end in the retainer clip and place the entire assembly on the hot end (metal) mount. Then take the two m3x12mm screws and tighten the entire assembly to the mount make sure you go through the extruder motor mount when doing this. If you didn’t melt the nuts into place take a putty knife and insert it between the part fan and the hot end mount – this will keep the nuts in place long enough for the screws to get a bite on the threads. Also ensure that the hot end is angled in such a fashion as to ensure that the least amount of surface area is adjacent to the part fan shroud.

Take the other extruder motor mount , two M3x10mm screws, and two m3 nuts and attach it to the plate on the opposite side of the extruder. Use nylon lock screws or a bit of blue lock tight on the threads to ensure that the screws stay in place.

Melt a M3 nut into the belt tension holder to ensure it doesn’t move. Install one end of the belt into the belt holder. At this point check to ensure that the belt will stay in place within the teeth of the belt holder. If it does not, then you should use some epoxy to glue down the belt. While this does prevent reuse of this belt holder and the belt it is preferable to having it pop out later. Now install the belt tension holder onto the extruder mount with the m3x10mm round button screws. You can optionally tap these holes prior to installing the belt holder

## Step 3 – Gantry

Tools needed

- 3mm allan key/wrench
- 2mm or 2.5 mm allen key/wrench
- Tape measure
- Dark colored sharpie
- square

Parts needed

- 2 4 hole c shaped support
- 2 triangle left handed 5 hole support
- 2 triangle right handed 5 hole support
- 4 15 inch vertical extrusion
- 2 17.5 inch horizontal extrusion
- 1 right hand z rod support
- 1 left hand z rod support
- 32 M5 extrusion nuts
- 48 M5 screws

Measure length of 4 extrusion and place a mark at 9” (half way) – take your measurement from the edge of the extrusion, not the plates. Take your square and draw a complete line at the 9” point. Measure inside of the c-shaped support. Make a mark at the 1.5” spot (half way) and square a line.

Drop 4 extrusion nuts into the top slot of the 4 rail high extrusion. Ensure these nuts align with the c support holes while the sharpie lines on the support and the extrusion are in alignment. You can do this by gently moving the nuts with the allen wrench. Once aligned tight down the screws into the nuts – make minor adjustments to ensure that the sharpie lines are aligned. Double check to make sure that the nuts are holding properly inside the rails of the extrusion. Perform same operation for the other side of the unit.

Now attach the vertical 15” extrusions to the plates you just attached. Don’t worry about making these square – lightly tighten down the nuts so they provide stability. Once the horizontal supports have been attached we’ll make these square.

Once the four vertical extrusion are in place install the z axis plates along with the horizontal extrusions. Once they are loosely screwed in now square the top of the vertical extrusions with the top horizontal extrusions. Tighly screw down the nuts. Now square the vertical extrusions with lower horizontal extrusions.

## Step 2 – Extruder and X-Axis Gantry / Z-axis

Tools needed

- 3mm allan key/wrench
- Square
- 10mm open ended wrench or adjustable wrench
- 8mm or another adjustable wrench

Parts needed

- 17” two high Al extrusion
- 2 arrow shaped supports
- 4 M5x25mm screws
- 2 M5x30mm screws.
- 6 vWheel kits
- 2 eccentric stand offs
- 4 smooth stand offs
- 6 M5 x 8mm button screws
- 4 M5 extrusion nuts
- 6 M5x25mm flat screws
- 6 M3 x 10mm button screws
- 6 M3 .05 pitch nuts
- 2 M5 Pulley kits

Install arrow head supports at the end of the Al extrusion. Make sure the arrow points are facing the same direction. Lightly tighten this parts as we’ll need some give in a later step.

Install the v-wheels. Start by installing the v-Wheels that are closets to the extruder/x-axis gantry. The screw should be installed so that the head of the screw is on the inside of the part. Then place the smooth stand off on the bolt, then the v-wheel (with the bearings installed), and then the nylon locking nut. Tighten this assembly down, but not too tight as the wheel should move freely. Be sure to avoid any ability for the vwheel to wooble on its axis. This is generally accomplished by tighting it down and then backing off a quarter turn Repeat this process for other three other remaining spots.

Now install the vwheel with the eccentric spacer. DO NOT attempt to install it on the gantry yet. You first want to get screw down the nut on the vwheel so that the eccentric spacer can seat all the way down in the hole provided by the support. Not do this will effectively make it impossible to install the wheel on the gantry. Once it has been seated evenly you can now unscrew the nut and take off the wheel. The eccentric spacer will stay in place after removing the screw. Rotate the spacer so that the widest edge is pointed toward the other wheels. This will help with installing the wheel in the next step. The screw should then slide through the support, the eccentric spacer, and the vwheel. Now tighten the nut as described above. Performm the same operation on the other side. At this point the gantry should move freely up and down.

You must remove any back and forth movement in the gantry (when facing the gantry) take the 10mm wrench and slowly adjust the eccentric spacer to remove any play in the gantry. This step should not inhibit the movement of the gantry, make sure the gantry can move up with out binding and drop easily without having to be pushed.

Install the x-axis / z-axis support on the extrusion. Use one pulley set on each side – the pulley should be on the outer hole on the side without the x-axis motor mount. The pulley should be on the inside of hole on the other side. The pulley should have a washer on either side of bearings, the nylon washer should go between the bearings. Don’t worry about tightening these down yet as they’ll be tighten when installing the z-axis motors. Ensure that the pins on the stepper motor point toward the hole on next to the stepper motor mount – these are used for cable management later.

Remove the z-axis nuts from the shaft of the stepper motor and then install the z-axis stepper motors on the top of the gantry by using the 8 M3 screws. Do not tighten down the z-axis motors.

Then with the help of a square tighten down the x/z axis mounts so that they are square and do not inhibit the z-axis from turning. This might require you to re-seat the z axis stepper motors for the optimal position between the mounts on the top of the gantry and the mounts for the x/z axis. This does not have to be perfect – as you will find out there’s a bit of wobble which prevents a perfect alignment. Once completed thread the z-axis nuts back on the threads. Screw them up until they hit the z-axis mount and attach them by using M3 x 10mm machine screws and the M3 nuts to screw them onto the z-axis nut and mount. Apply a bit of blue lock-tite on the threads of the screw to ensure that the nuts hold in place. It will take some effort to maneuver the M3 nuts under the z axis nuts – so seat the screws up through the bottom and then attach nuts on the top. However, it is possible to attach the nuts from the bottom – it just requires a magnetic screw driver to hold the nut in place while you drive the M3 screw into it. Once this has been done you can now tighten the z-axis motors on the top of the gantry. Manually move the x axis/extruder gantry about 50% up from the resting position – this will give you some room to install the y-axis in a later step.

## Step 3 – Extruder and X-Axis Mounting Plate

This should occur after the gantry and after the plate has been populated above.

Tools needed

- 3mm allan key/wrench
- Square
- 10mm open ended wrench or adjustable wrench
- 8mm or another adjustable wrench
- 2.5mm allan key/wrench

Parts needed

- One large v-wheel kit
- Two small v-wheel kit
- Two Al spacer
- One off set spacer
- Three M5x25mm flat head screws
- 4 M3x8mm button screws
- Stepper motor

Take extruder/x-axis mounting plate, offset spacer, and the large v-wheel kit. Assemble the large v-wheel - push the screw through the larger hole at the end of the mount and place the off set spacer on the opposite side of the plate. Then place the wheel on the offset nut then place and screw down the nut on wheel until the offset nut completely seats on the plate. Remove the large wheel and then adjust the offset nut so that the large edge points toward the small end of the plate.

Install the two smaller v-wheels on the plate. Place the screw into the smaller holes opposite the offset spacer. On the other side place the Al spacer, one washer (from the kit), the small v-wheel, another small washer and then the nut. Repeat for the second small v-wheel. Tighten the nuts on the wheel until there is no play (or wobble) in the wheel while still allowing it to spin freely. Once this is complete, reassemble the large v-wheel while holding the plate over the extruder/x-axis gantry. Before tightening the nut on the large v-wheel down make sure that all the wheels are set in the top groove of the gantry. Once the nut is set on the large wheel slowly adjust the offset spacer so that the plate can move freely but provide little to no play vertically while being pushed across the gantry horizontonally.

Once complete the extruder/x-axis mount should move freely in the horizotonal direction along the gantry.

Install the x-axis stepper motor using 4 M3x8m screws. Ensure that the power cable mount is facing toward the center of the gantry along the x-axis.

At this point you can attach the stepper motor 20 tooth (or your preferred size) pulley and the GT2 belt. You will have to trim the belt a bit and attach the other end to the belt connector. If there is any movement of the belt in the belt connector you will have to put some epoxy on this end too and allow to dry. After you get the belt connector in the connector body tighten the belt so that the extruder head exhibits no slop when moving the head back and forth – for every movement of the print head there should be movement of the stepper motor. This can be checked by holding onto the stepper motor pulley while pushing the extruder assembly – as you hold the pulley tightly the extruder head should not move when pushed or pulled gently.

## Step 4 – Y-Axis

Tools needed

- 3mm allan key/wrench
- Square
- Black sharpie
- 8mm wrench or socket
- 10mm open ended wrench

Parts needed

- 8 M5 x 8mm button screws
- 4 M5 x 25mm tall button screws
- 4 M5 extrusion nuts
- 2 18” extrusions
- Small and large y-axis plates
- 2 offset spacers
- 2 normal spacers
- 4 large v-wheel kits

Find the center point for both the extrusions on the front and back of the printer. Also find the center point for both y-axis plates. Install the plates on to the frame of the printer using the topmost portion of the extrusion. Ensure that the center lines are aligned and that the plate is square to the frame.

Place both 18” extrusions across the middle of the frame, use the M5 button screws to lightly screw down the extrusions. Only tighten one of the extrusions completely – make sure that it is square with the frame as well as sitting firmly on the top of the frame. If you find yours are a bit off the frame, adjust the y-axis plates until the y-axis extursions are sitting on top of the frame. Leave the other y-axis extrusion slightly loose for the next step.

## Step 5 – Y-axis mounting plate

Tools needed

- 8mm wrench or socket
- 3mm allen wrechn
- 10mm open ended wrech

Parts needed

- 4 large v-wheel kits
- 4 M5x25mm screw
- 4 M5 nylon nuts
- 2 Al spacers
- 2 offset spacers
- Y-axis mounting plate

Install two large v-wheels on y-axis mounting plate. Push the bolt through the smaller hole toward the center of the plate, place the normal spacer on the other side of the place, then the v-wheel, the place the nylon nut on the screw. Repeat for the other side. ensure that the nuts are tightened enough to prevent the screw from wobbling, but allows the bears spin freely.

Turn your printer on its side now and place the plate in a position where the v-wheels are sitting in the rail positions. Now install in the other wheels using the offset spacers, again making sure that the bearings are free to move – during this step it is important that the wheels remain in the groove of the y-axis extursion. Then spin the offset spacers so that the y-axis mounting plate moves freely but does not move outside of the grooves of the extrusion. Also during this step it is important to tighten down the y-axis extrusion. It might take a few tries between adjusting the offset spacers and positioning of the y-axis extrusion to allow the y-axis mount free movement. However, when you are complete the plate should move freely without binding at any position on the extrusion.

## Step 6 –Install axis electronics

Tools needed

- 2.5mm allen wrench

Parts needed

- 6 M3x8mm button screws
- Stepper motor
- Y-axis stepper motor mounting plate
- 2 pulley kit
- 4 M5 extrusion nuts
- 3 M5x8mm screw
- 2 M5x30mm screw
- 2 Al ¼” spacer
- 3 M5 washers (you’ll have a few left over)

Indentify from the last step the side in which the y-axis mounting screw holes are on the build plate mount. You will want to install the two pullies and y-axis stepper motor on the y-axis extrusion rail that is on the same side.

Use the four M3 screws to secure the stepper motor to the y-axis belt mount. Place two M5 extrusion nuts toward one end of the extrusion rail. Then use one M5x8mm screw and extrusion M5 nut to attach the plate to the y-axis extrusion rail. Push one of the M5x30 nut through a belt pulley and attach the ¼” spacer to the other side of the pulley. Push this assembly through the stepper motor plate and screw down securely into the M5 extrusion nut. Aseemble another M5 pully – this time placing the ¼” spacer and three washers on the other side of the pully. Then screw into the rail using another M5 extrusion nut toward the other end of the rail. Keep enough space for you to be able to feed the belt around the pulley.

Now assemble the Y end stop mount. Secure the end stop break out board with 2 m3x8mm screws. Now take the M5x8mm and extrusion nut and attach the end stop assembly onto the frame near the y axis motor. Test operation of this end stop by making sure the switch is triggered when the v-wheel comes into contact with the switch.

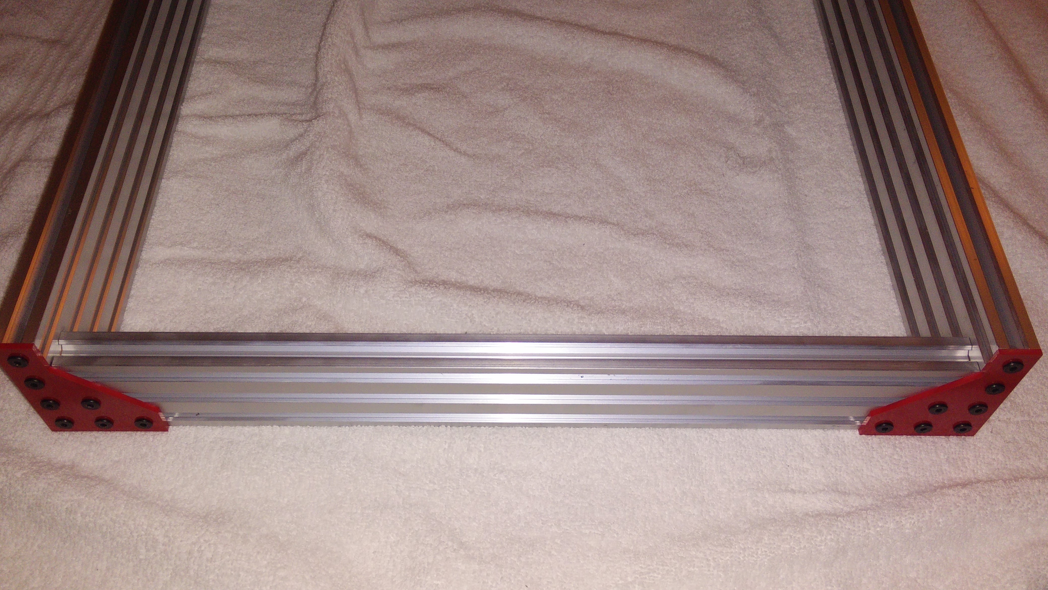
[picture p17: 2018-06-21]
Spartan/Pictures and Video/Assembly Images/IMG_20151223_195312.jpg

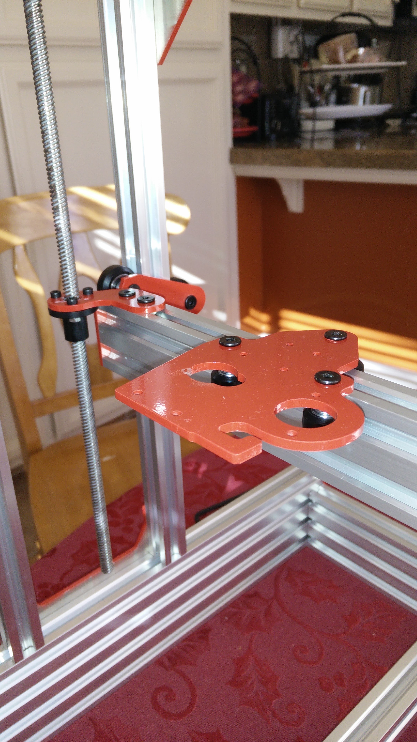
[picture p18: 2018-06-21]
Spartan/Pictures and Video/Assembly Images/IMG_20151231_123420.jpg

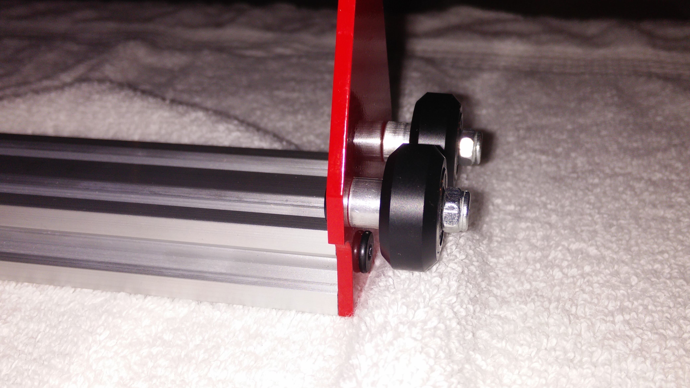
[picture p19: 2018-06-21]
Spartan/Pictures and Video/Assembly Images/IMG_20151224_173850.jpg

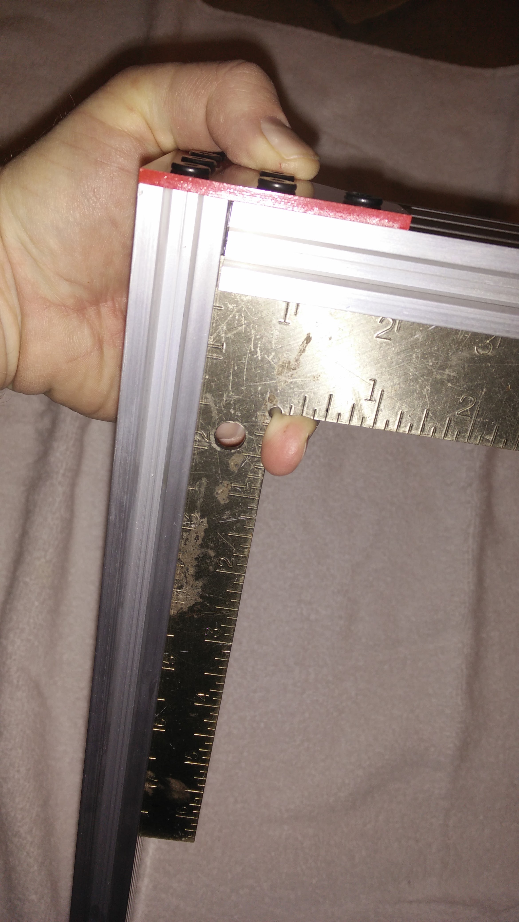
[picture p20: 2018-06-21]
Spartan/Pictures and Video/Assembly Images/IMG_20151223_194639.jpg

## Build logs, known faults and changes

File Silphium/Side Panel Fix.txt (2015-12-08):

( Side Panel Fix )
( File created: Sunday, November 29, 2015 - 11:19 PM)
( for Mach2/3 from Vectric )
( Material Size)
( X= 85.000, Y= 190.000, Z= 4.000)
()
(Toolpaths used in this file:)
(Profile 4)
(Profile 3)
(Tools used in this file: )
(1 = End Mill {0.125 inch})
N110G00G21G17G90G40G49G80
N120G71G91.1
N130T1M06
N140 (End Mill {0.125 inch})
N150G00G43Z5.000H1
N160S12000M03
N170(Toolpath:- Profile 4)
N180()
N190G94
N200X0.000Y0.000F1270.0
N210G00X18.000Y35.787Z3.000
N220G00Z0.500
N230G1Z-3.250F50.8
N240G2X16.788Y37.000I0.000J1.213F1270.0
N250G2X18.000Y38.213I1.212J0.000
N260G2X19.212Y37.000I0.000J-1.213
N270G2X18.000Y35.787I-1.212J0.000
N280G1Z-3.500F50.8
N290G2X16.788Y37.000I0.000J1.213F1270.0
N300G2X18.000Y38.213I1.212J0.000
N310G2X19.212Y37.000I0.000J-1.213
N320G2X18.000Y35.787I-1.212J0.000
N330G1Z-3.750F50.8
N340G2X16.788Y37.000I0.000J1.213F1270.0
N350G2X18.000Y38.213I1.212J0.000
N360G2X19.212Y37.000I0.000J-1.213
N370G2X18.000Y35.787I-1.212J0.000
N380G00Z3.000
N390G00X10.000Y51.787
N400G00Z0.500
N410G1Z-3.250F50.8
N420G2X8.788Y53.000I0.000J1.213F1270.0
N430G2X10.000Y54.213I1.212J0.000
N440G2X11.212Y53.000I0.000J-1.213
N450G2X10.000Y51.787I-1.212J0.000
N460G1Z-3.500F50.8
N470G2X8.788Y53.000I0.000J1.213F1270.0
N480G2X10.000Y54.213I1.212J0.000
N490G2X11.212Y53.000I0.000J-1.213
N500G2X10.000Y51.787I-1.212J0.000
N510G1Z-3.750F50.8
N520G2X8.788Y53.000I0.000J1.213F1270.0
N530G2X10.000Y54.213I1.212J0.000
N540G2X11.212Y53.000I0.000J-1.213
N550G2X10.000Y51.787I-1.212J0.000
N560G00Z3.000
N570G00Y71.787
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
(Profile 3)
()
N2760G00X-1.587Y20.000Z3.000
N2770G00Z0.500
N2780G1Z-3.250F50.8
N2790G3X20.000Y-1.587I21.587J0.000F1270.0
N2800G1X35.619
N2810G1Z-3.000
N2820G1X40.294
N2830G1Z-3.250F50.8
N2840G1X60.000F1270.0
N2850G3X81.588Y20.000I0.000J21.587
N2860G1Y36.825
N2870G1Z-3.000
N2880G1Y41.500
N2890G1Z-3.250F50.8
N2900G1Y53.000F1270.0
N2910G3X45.000Y89.588I-36.588J0.000
N2920G1X29.216
N2930G1Z-3.000
N2940G1X24.541
N2950G1Z-3.250F50.8
N2960G1X7.000F1270.0
N2970G3X-1.587Y81.000I0.000J-8.588
N2980G1Y47.950
N2990G1Z-3.000
N3000G1Y43.275
N3010G1Z-3.250F50.8
N3020G1Y20.000F1270.0
N3030G1Z-3.500F50.8
N3040G3X20.000Y-1.587I21.587J0.000F1270.0
N3050G1X35.619
N3060G1Z-3.000
N3070G1X40.294
N3080G1Z-3.500F50.8
N3090G1X60.000F1270.0
N3100G3X81.588Y20.000I0.000J21.587
N3110G1Y36.825
N3120G1Z-3.000
N3130G1Y41.500
N3140G1Z-3.500F50.8
N3150G1Y53.000F1270.0
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
%

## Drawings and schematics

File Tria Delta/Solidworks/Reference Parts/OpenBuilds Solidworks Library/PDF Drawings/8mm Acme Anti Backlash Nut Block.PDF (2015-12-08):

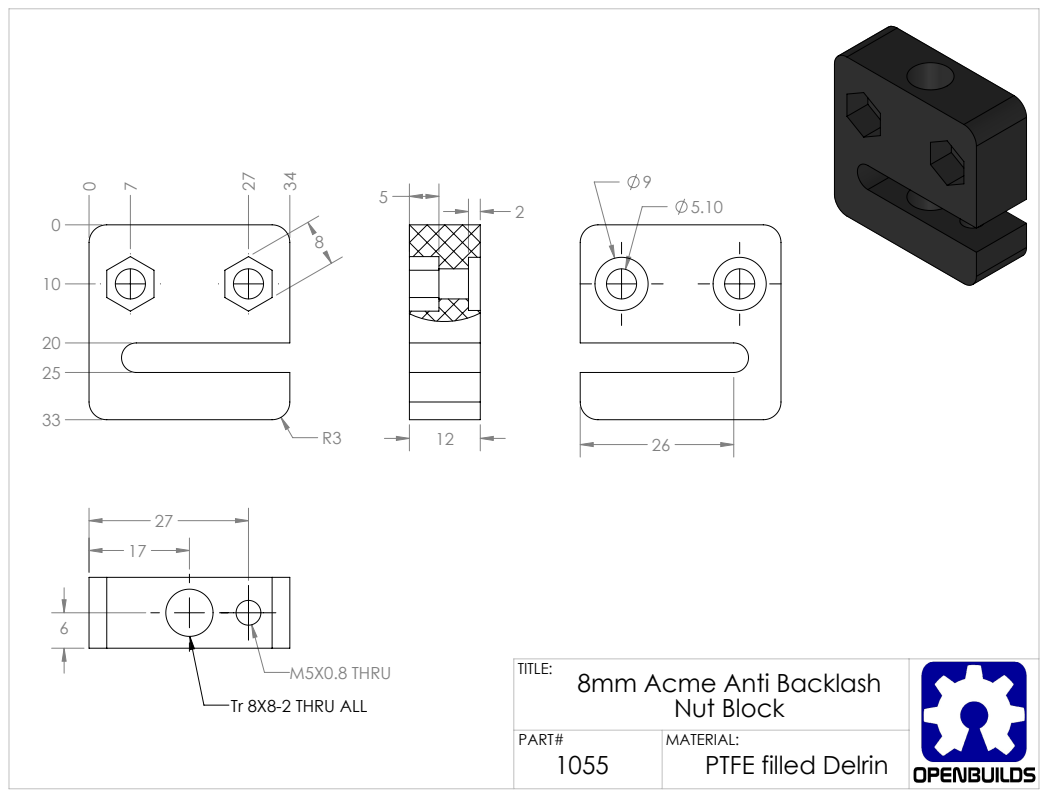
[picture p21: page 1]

M5X0.8 THRU
Tr 8X8-2 THRU ALL

TITLE: 8mm Acme Anti Backlash Nut Block

PART# 1055 | MATERIAL: PTFE filled Delrin

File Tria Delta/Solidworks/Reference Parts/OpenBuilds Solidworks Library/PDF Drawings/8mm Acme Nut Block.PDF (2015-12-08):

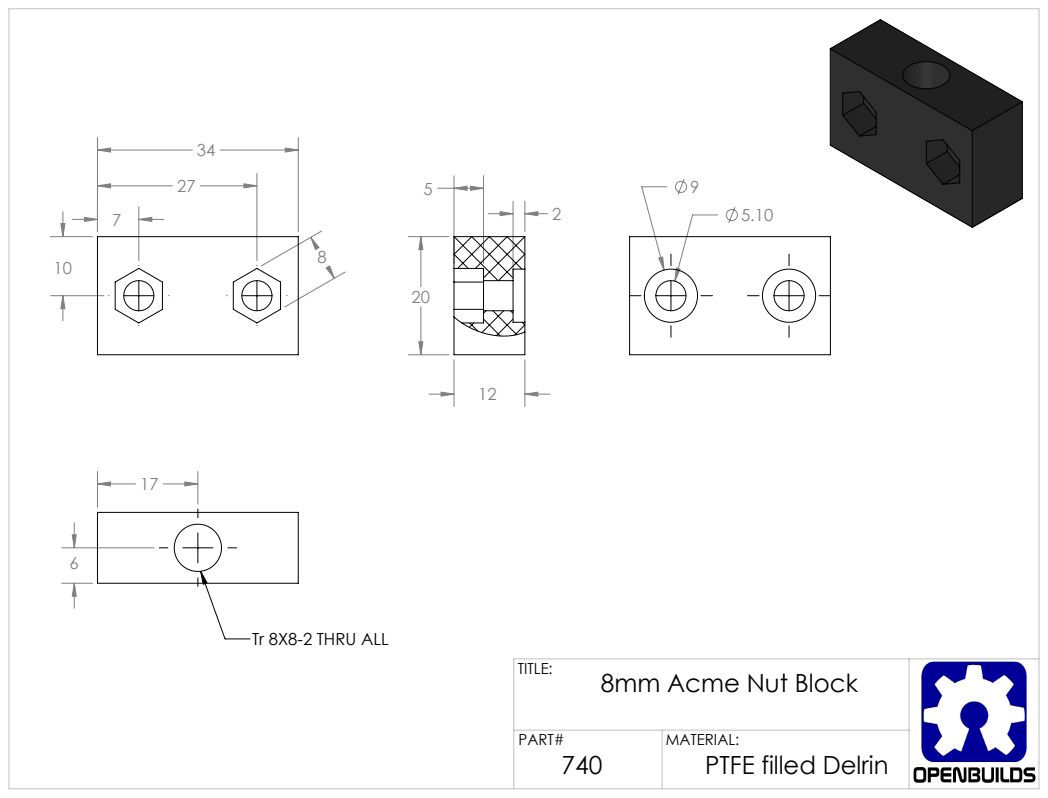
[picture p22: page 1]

Tr 8X8-2 THRU ALL

TITLE: 8mm Acme Nut Block

PART# 740 | MATERIAL: PTFE filled Delrin

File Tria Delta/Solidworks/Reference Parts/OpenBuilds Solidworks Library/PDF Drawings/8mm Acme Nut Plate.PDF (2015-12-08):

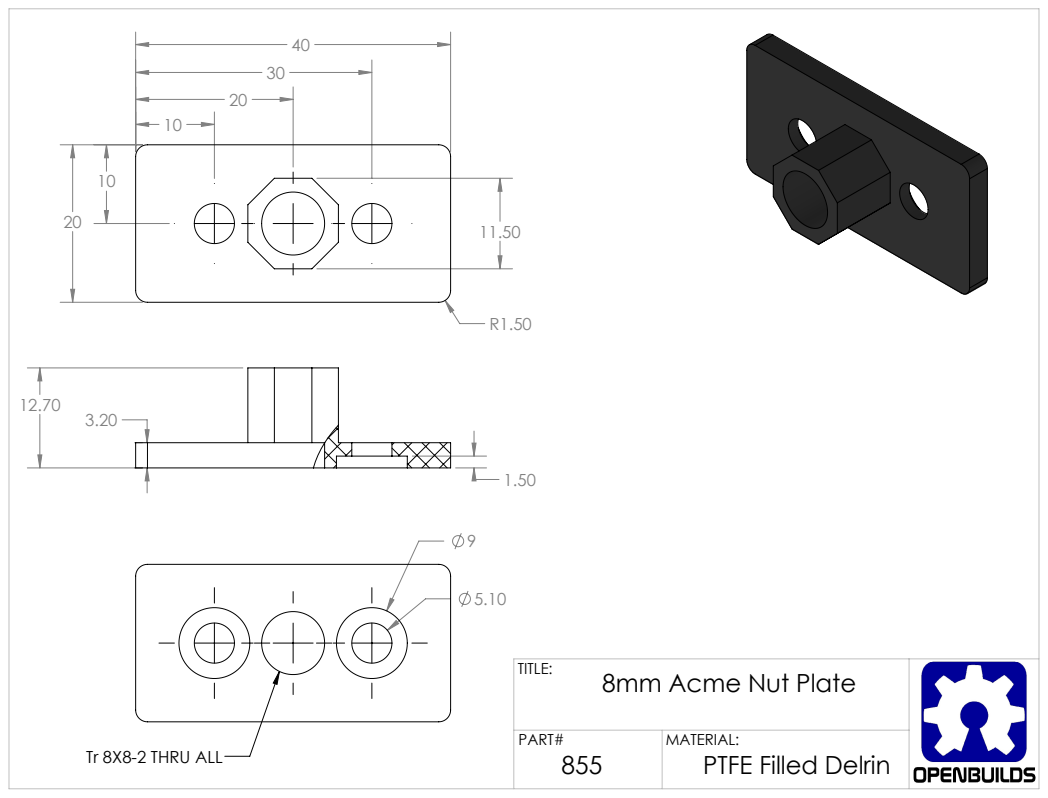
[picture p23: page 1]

TITLE: 8mm Acme Nut Plate

PART# 855 | MATERIAL: PTFE Filled Delrin

Tr 8X8-2 THRU ALL

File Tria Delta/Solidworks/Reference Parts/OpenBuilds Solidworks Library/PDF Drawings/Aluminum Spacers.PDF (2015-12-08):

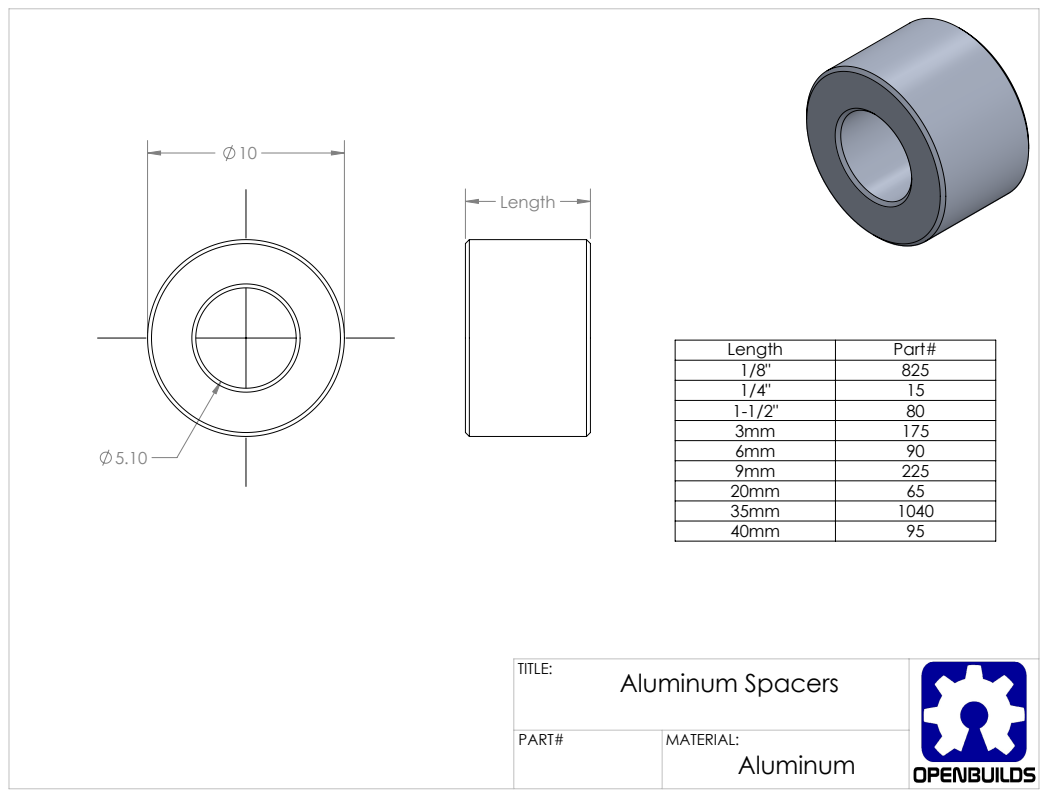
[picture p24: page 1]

Length | Part#
1/8" | 825
1/4" | 15
1-1/2" | 80
3mm | 175
6mm | 90
9mm | 225
20mm | 65
35mm | 1040
40mm | 95

TITLE: Aluminum Spacers

PART# | MATERIAL: Aluminum

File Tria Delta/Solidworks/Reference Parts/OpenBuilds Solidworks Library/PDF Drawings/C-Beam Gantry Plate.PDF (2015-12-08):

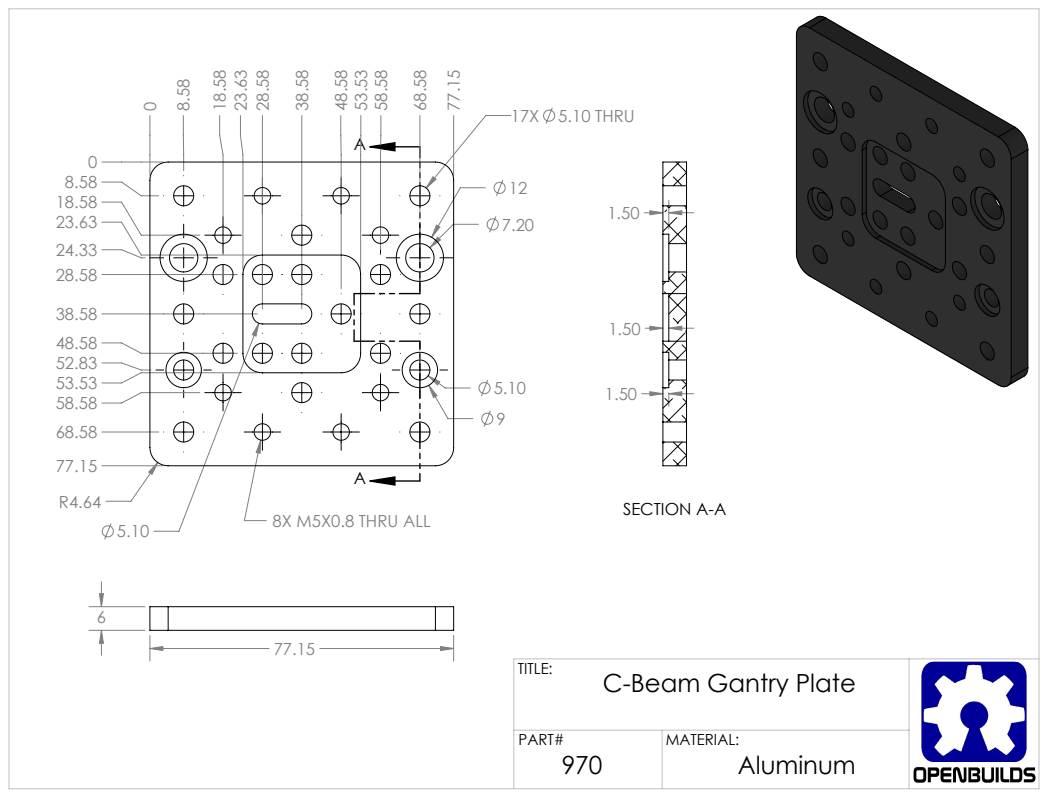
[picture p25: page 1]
8X M5X0.8 THRU ALL; 17X 5.10 THRU; SECTION A-A

TITLE: C-Beam Gantry Plate

PART# 970 | MATERIAL: Aluminum

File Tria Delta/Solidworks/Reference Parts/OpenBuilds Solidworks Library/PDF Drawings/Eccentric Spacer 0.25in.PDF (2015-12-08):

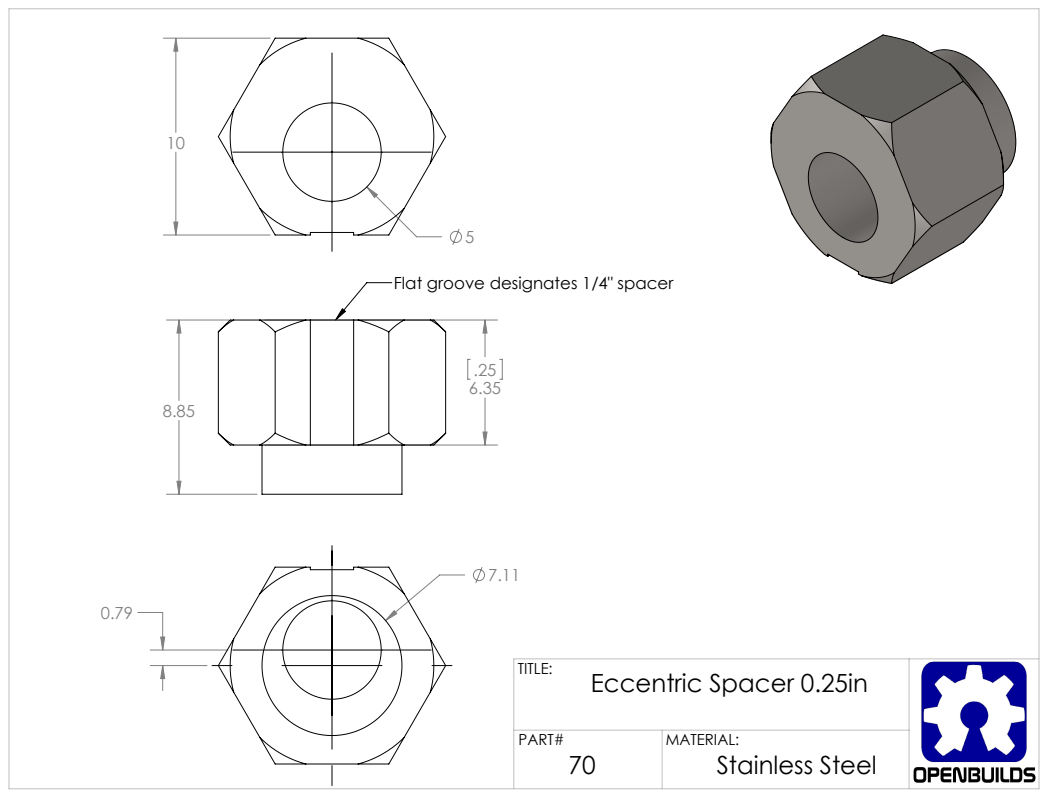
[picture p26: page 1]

Flat groove designates 1/4" spacer

TITLE: Eccentric Spacer 0.25in

PART# 70 | MATERIAL: Stainless Steel

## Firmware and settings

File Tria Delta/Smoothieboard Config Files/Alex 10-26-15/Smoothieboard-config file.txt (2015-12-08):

# NOTE Lines must not exceed 132 characters
# Robot module configurations : general handling of movement G-codes and slicing into moves
default_feed_rate                            12000             # Default rate ( mm/minute ) for G1/G2/G3 moves
default_seek_rate                            12000             # Default rate ( mm/minute ) for G0 moves
mm_per_arc_segment                           0.5              # Arcs are cut into segments ( lines ), this is the length for
                                                              # these segments.  Smaller values mean more resolution,
                                                              # higher values mean faster computation
#mm_per_line_segment                         0.5              # Lines can be cut into segments ( not useful with cartesian
                                                              # coordinates robots ).
delta_segments_per_second                    400              # for deltas only same as in Marlin/Delta, set to 0 to disable
                                                              # and use mm_per_line_segment


# Arm solution configuration : Cartesian robot. Translates mm positions into stepper positions
arm_solution                                 linear_delta     # selects the delta arm solution
alpha_steps_per_mm                           80              # Steps per mm for alpha stepper
beta_steps_per_mm                            80              # Steps per mm for beta stepper
gamma_steps_per_mm                           80              # Steps per mm for gamma stepper

arm_length                                   288.2#289.0            # this is the length of an arm from hinge to hinge
arm_radius                                   174.6            # this is the horizontal distance from hinge to hinge
                                                              # when the effector is centered

# Planner module configuration : Look-ahead and acceleration configuration
planner_queue_size                           32               # DO NOT CHANGE THIS UNLESS YOU KNOW EXACTLY WHAT YOU ARE DOING
acceleration                                 9000             # Acceleration in mm/second/second.
acceleration_ticks_per_second                1000             # Number of times per second the speed is updated
junction_deviation                           0.1             # Similar to the old "max_jerk", in millimeters,
                                                              # see https://github.com/grbl/grbl/blob/master/planner.c#L409
                                                              # and https://github.com/grbl/grbl/wiki/Configuring-Grbl-v0.8
                                                              # Lower values mean being more careful, higher values means being
                                                              # faster and have more jerk
#minimum_planner_speed                       0.0              # sets the minimum planner speed in mm/sec

# Stepper module configuration
microseconds_per_step_pulse                  1                # Duration of step pulses to stepper drivers, in microseconds
base_stepping_frequency                      100000           # Base frequency for stepping, higher gives smoother movement

# Cartesian axis speed limits
x_axis_max_speed                             30000            # mm/min
y_axis_max_speed                             30000            # mm/min
z_axis_max_speed                             30000            # mm/min

# Stepper module pins ( ports, and pin numbers, appending "!" to the number will invert a pin )
alpha_step_pin                               2.0              # Pin for alpha stepper step signal
alpha_dir_pin                                0.5              # Pin for alpha stepper direction
alpha_en_pin                                 0.4              # Pin for alpha enable pin
alpha_current                                1.0              # X stepper motor current
alpha_max_rate                               30000.0          # mm/min

beta_step_pin                                2.1              # Pin for beta stepper step signal
beta_dir_pin                                 0.11             # Pin for beta stepper direction
beta_en_pin                                  0.10             # Pin for beta enable
beta_current                                 1.0              # Y stepper motor current
beta_max_rate                                30000.0          # mm/min

gamma_step_pin                               2.2              # Pin for gamma stepper step signal
gamma_dir_pin                                0.20             # Pin for gamma stepper direction
gamma_en_pin                                 0.19             # Pin for gamma enable
gamma_current                                1.0              # Z stepper motor current
gamma_max_rate                               30000.0          # mm/min

# Serial communications configuration ( baud rate default to 9600 if undefined )
uart0.baud_rate                              250000           # Baud rate for the default hardware serial port
second_usb_serial_enable                     false            # This enables a second usb serial port (to have both pronterface
                                                              # and a terminal connected)
#leds_disable                                true             # disable using leds after config loaded
#msd_disable                                 false            # disable the MSD (USB SDCARD) when set to true

# Extruder module configuration
extruder.hotend.enable                          true             # Whether to activate the extruder module at all. All configuration is ignored if false
extruder.hotend.steps_per_mm                    475              # Steps per mm for extruder stepper
extruder.hotend.default_feed_rate               600              # Default rate ( mm/minute ) for moves where only the extruder moves
extruder.hotend.acceleration                    500              # Acceleration for the stepper motor, as of 0.6, arbitrary ratio
extruder.hotend.max_speed                       100               # mm/s

extruder.hotend.step_pin                        2.3              # Pin for extruder step signal
extruder.hotend.dir_pin                         0.22             # Pin for extruder dir signal
extruder.hotend.en_pin                          0.21             # Pin for extruder enable signal

# extruder offset
#extruder.hotend.x_offset                        0                # x offset from origin in mm
#extruder.hotend.y_offset                        0                # y offset from origin in mm
#extruder.hotend.z_offset                        0                # z offset from origin in mm

# firmware retract settings when using G10/G11, these are the defaults if not defined, must be defined for each extruder if not using the defaults
#extruder.hotend.retract_length                  6               # retract length in mm
#extruder.hotend.retract_feedrate                60              # retract feedrate in mm/sec
#extruder.hotend.retract_recover_length          0               # additional length for recover
#extruder.hotend.retract_recover_feedrate        8               # recover feedrate in mm/sec (should be less than retract feedrate)
#extruder.hotend.retract_zlift_length            0.40               # zlift on retract in mm, 0 disables
#extruder.hotend.retract_zlift_feedrate          6000            # zlift feedrate in mm/min (Note mm/min NOT mm/sec)

delta_current                                    1.00              # First extruder stepper motor current

# Second extruder module configuration example
#extruder.hotend2.enable                          true             # Whether to activate the extruder module at all. All configuration is ignored if false
#extruder.hotend2.steps_per_mm                    140              # Steps per mm for extruder stepper
#extruder.hotend2.default_feed_rate               600              # Default rate ( mm/minute ) for moves where only the extruder moves
#extruder.hotend2.acceleration                    500              # Acceleration for the stepper motor, as of 0.6, arbitrary ratio
#extruder.hotend2.max_speed                       50               # mm/s

#extruder.hotend2.step_pin                        2.8              # Pin for extruder step signal
#extruder.hotend2.dir_pin                         2.13             # Pin for extruder dir signal
#extruder.hotend2.en_pin                          4.29             # Pin for extruder enable signal
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

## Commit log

2015-12-08 First Commit
    First Commit
    [10x10_Dragchain_A.stl, 10x10_Dragchain_B.stl, 10x10_Dragchain_C.stl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]
2015-12-08 SilPhium and Tria Delta
    [1X End Effector.STL, 1X Extruder Bracket.STL, 1X Extruder Pressure Fixture.STL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]
2015-12-09 creating new configurable M4 screw + T-nut assembly
    [M4_Low_Profile_Screw_with_T_nut.SLDASM, Tee Nut M4.SLDPRT]
2015-12-09 adding new configurable screw + t nut to the one third assembly
    [40MM_NEMA17.SLDASM, Low Profile Screw M4.SLDPRT, Lower Vertex.SLDASM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]
2015-12-09 deleting other references.
    [1X End Effector.STL, 1X Extruder Bracket.STL, 1X Extruder Pressure Fixture.STL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]
2016-04-17 Add New Light Weight Effector
    User Mod - Eric Lien
    1.) Add New Light Weight Effector
    2.) Add Bungee retention method to avoid effector getting knocked off
    Models in Solidworks and many other formats
    [30x30_Fan.SLDASM, 3mm_Hex_Nut.sldprt, 4020Blower.SLDPRT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]
2016-09-25 Updated X-Carriage Universal, with offset
    [X Carriage Universal.DXF]
2016-10-02 Clean Up
    Cleaned up the STLs for printing.
    [Bed Clip For Glass.STL, Belt Connector Body.STL, Belt Connector.STL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]
2018-02-03 added assembly instructions and some images that go with assembly instructions.
2018-06-21 Finished Tria Delta Model
    Finally Finished the Tria Delta 3D Model, and repaired some errors on Spartan.
    [10in Round PEI SHeet.SLDPRT, 12MHZ Crystal PN X322512MMB4SC.sldprt, 12V.PSU.Cover (1).STL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]
2018-06-21 Fix User Mod Name
    For some reason the user mod folder had sss added to my name
    [30x30_Fan.SLDASM, 3mm_Hex_Nut.sldprt, 4020Blower.SLDPRT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]
